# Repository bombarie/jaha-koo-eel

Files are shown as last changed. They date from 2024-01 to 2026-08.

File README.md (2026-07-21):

# Jaha Koo Eel

A robotic remote controlled eel. A prop for the play [Haribo Kimchi](https://www.campo.nu/en/production/24342/haribo_kimchi).

A collaboration between [Adriaan Wormgoor](http://adriaanwormgoor.nl) and [Willem Vooijs](https://willem.vooijs.eu), produced for [Innovation:Lab Theater Utrecht](https://www.theaterutrecht.nl/innovationlab) and [Campo](https://campo.nu).

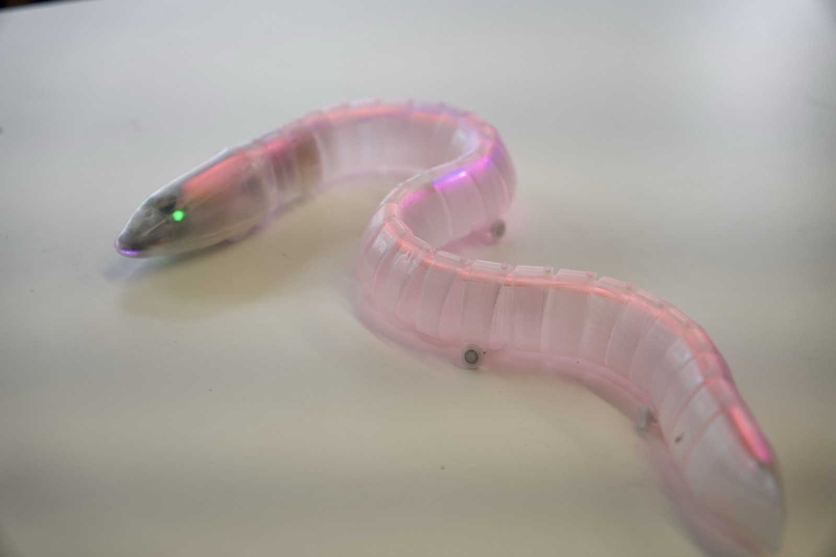
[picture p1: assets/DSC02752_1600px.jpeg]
haribo


## Manual
* [Operator Manual](doc/Haribo%20Kimchi%20Eel%20-%20operator%20manual.pdf)

## Build your own
* [Bill of Materials](./BOM.md)
* [Schematics](doc/Haribo%20Kimchi%20Eel%20-%20tech%20stuff%20-%20visual%20schematic%20and%20pinout.pdf)
* [Code](./arduino/README.md)
* [PCB designs](./kicad/README.md)

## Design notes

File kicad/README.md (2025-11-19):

# PCB Design - quick Links

> 💡 Note the **[libraries](./libraries/)** folder, containing some custom-developed _footprints_ and _symbols_ which are used in various Kicad projects in this repository 

### PCB inside the Eel

[Kicad project](./eel_head_pcbs_assembly//eel_esp32_switch_host_board_v02/)\
[Gerber files](./eel_head_pcbs_assembly/eel_esp32_switch_host_board_v02/_export/gerberfiles/aisler_v01.zip)\
[Schematic](./eel_head_pcbs_assembly/eel_esp32_switch_host_board_v02/_export/schematics/Haribo%20Kimchi%20-%20Eel%20mainboard.pdf)

### PCB inside the GEPRC Tinyradio ELRS r/c transmitter

[Kicad project](./Teensy_32_tx_breakout_board_v2/)\
[Gerber files](./Teensy_32_tx_breakout_board_v2/_export/gerberfiles/jlcpcb_v0.3.zip)\
[Schematic](./Teensy_32_tx_breakout_board_v2/_export/schematics/Teensy%203.2%20host%20pcb.pdf)

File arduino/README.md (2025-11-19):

# Arduino code

All sketches where developed in VSCode using the Platformio plugin.

There's a _lot_ of scrappy test projects, so find below a quick link to the most recent version of key sketches

### Main sketch for Eel microcontroller

[main_seeed_xiao_esp32c3_v2_w_external_files.cpp](./platformio/esp32c3_helloworld/esp32c3_helloworld/src/main_seeed_xiao_esp32c3_v2_w_external_files.cpp)

### Main sketch for Teensy 3.2 inside the GEPRC Tinyradio r/c transmitter

[main.cpp](./platformio/TeensyDuino/src/main.cpp)

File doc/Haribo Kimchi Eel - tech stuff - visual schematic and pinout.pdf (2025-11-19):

# XIAO ESP32-C3

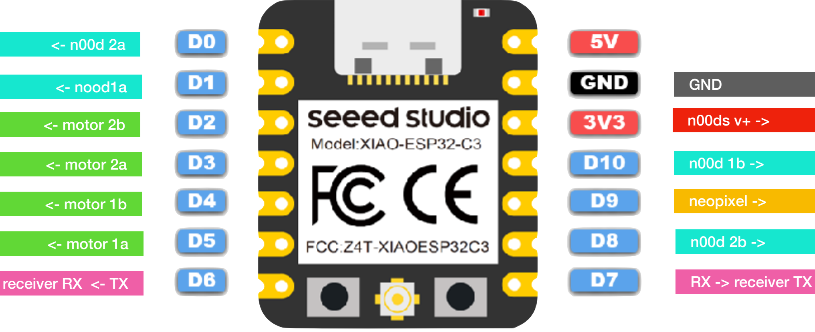
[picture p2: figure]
receiver RX <- TX; RX -> receiver TX; <- motor 2b; <- motor 2a; neopixel ->; <- nood1a
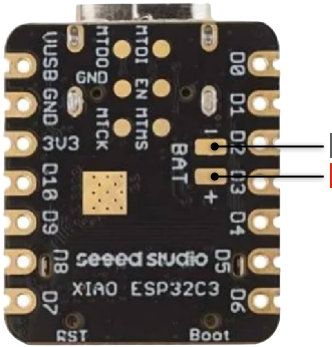
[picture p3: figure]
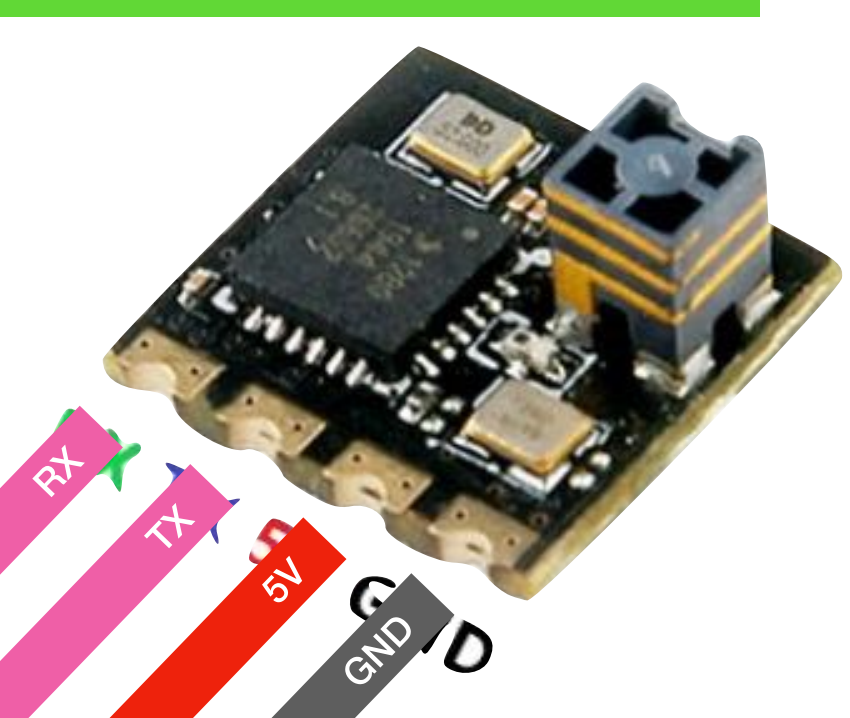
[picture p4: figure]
GND

Bat +

Bat - / GND

<- motor 1b

<- motor 1a

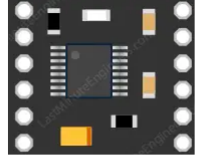
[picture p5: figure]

GND

<- motor 1 +

<- motor 1 -

5V

motor 2b <-

# Generic DRV8833 motor driver

GND
<- motor 2 +

<- motor 2 -

motor 2a <-

motor 1b <-

motor 1a <-

# Happymodel EP2 TXCO ELRS rx

# 600ma 5v boost converter

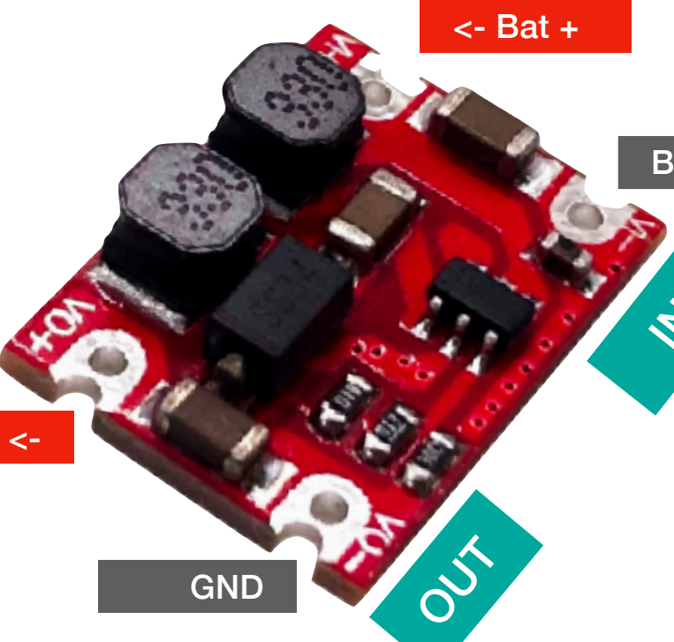
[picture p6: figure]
GND; <- Bat +; OUT

5V <-

Bat GND

IN

# XIAO ESP32-C3

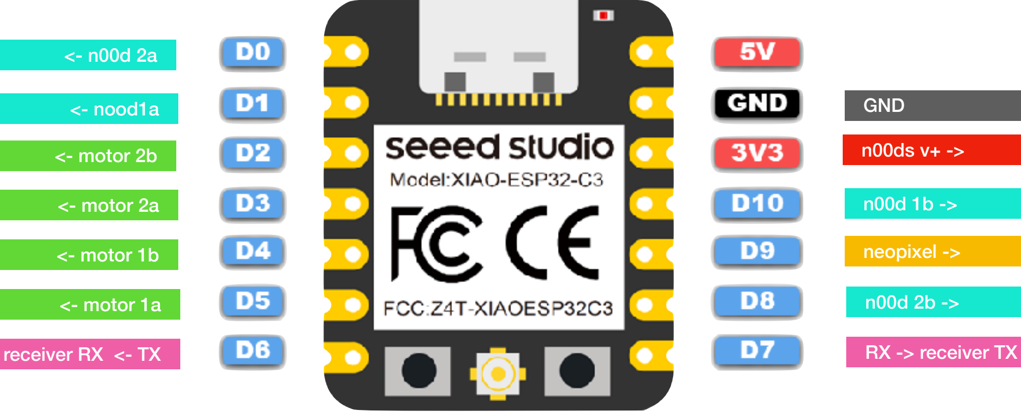
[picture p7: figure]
receiver RX <- TX; RX -> receiver TX; <- motor 2b; <- motor 2a; neopixel ->; <- nood1a
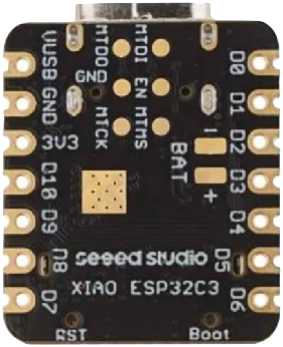
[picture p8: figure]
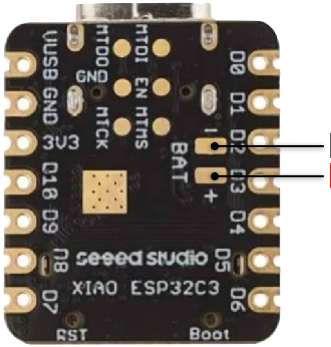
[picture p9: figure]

Bat +

Bat - / GND

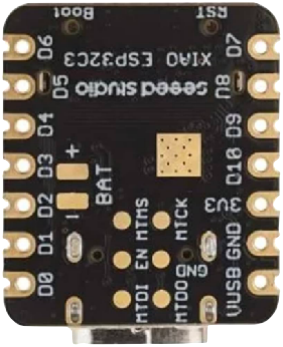
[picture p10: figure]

<- motor 1b

<- motor 1a

GND

<- motor 1b

<- motor 1a

receiver RX <- TX

<- motor 2b

<- motor 2a

<- nood1a

<- n00d 2a

GND

RX -> receiver TX

neopixel ->

n00d 2b ->

n00d 1b ->

n00ds v+ ->

GND

RX -> receiver TX

neopixel ->

n00d 2b ->

n00d 1b ->

n00ds v+ ->

<- motor 1b

<- motor 1a

receiver RX <- TX

<- motor 2b

<- motor 2a

<- nood1a

<- n00d 2a

# Comm protocol of n00ds

# * Midi is 0-127

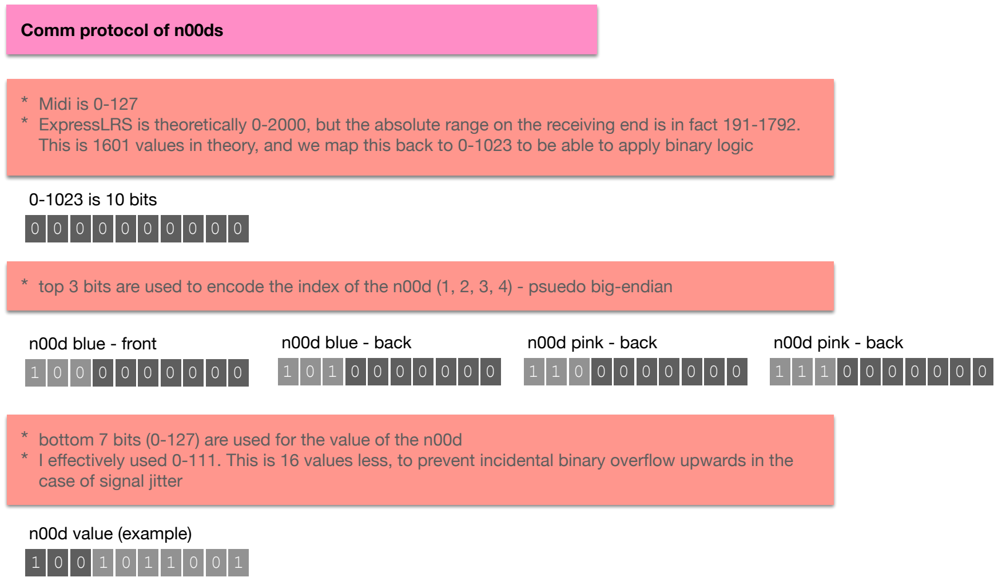
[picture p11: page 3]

0 | 0 | 0 | 0 | 0 | 0 | 0 | 0 | 0 | 0

# 0-1023 is 10 bits

1 | 0 | 0 | 0 | 0 | 0 | 0 | 0 | 0 | 0

# n00d blue - front

1 | 0 | 1 | 0 | 0 | 0 | 0 | 0 | 0 | 0

# n00d blue - back

1 | 1 | 0 | 0 | 0 | 0 | 0 | 0 | 0 | 0

# n00d pink - back

1 | 1 | 1 | 0 | 0 | 0 | 0 | 0 | 0 | 0

# n00d pink - back

* ExpressLRS is theoretically 0-2000, but the absolute range on the receiving end is in fact 191-1792. This is 1601 values in theory, and we map this back to 0-1023 to be able to apply binary logic

# * top 3 bits are used to encode the index of the n00d (1, 2, 3, 4) - psuedo big-endian

# * bottom 7 bits (0-127) are used for the value of the n00d

* I effectively used 0-111. This is 16 values less, to prevent incidental binary overflow upwards in the

# case of signal jitter

1 | 0 | 0 | 1 | 0 | 1 | 1 | 0 | 0 | 1

# n00d value (example)

# AUX4

# AUX3

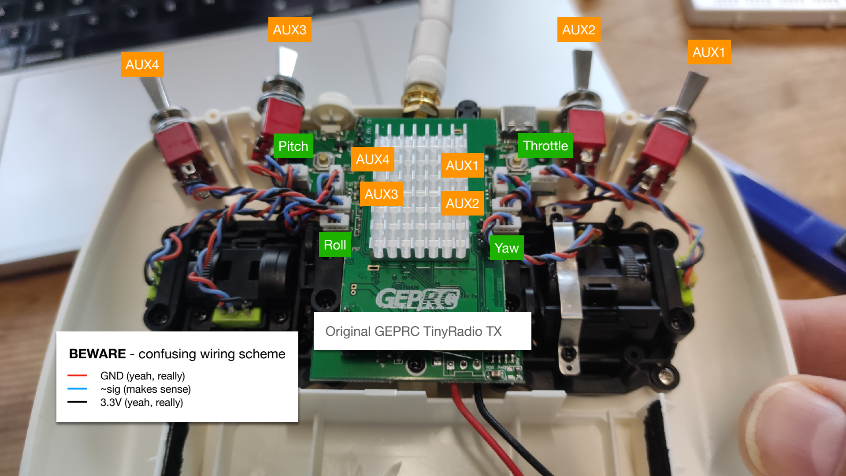
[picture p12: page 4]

# Pitch AUX4

# AUX3

Roll | Yaw

# Throttle AUX1

# AUX1

# AUX2

# AUX2

# Original GEPRC TinyRadio TX BEWARE - confusing wiring scheme

## GND (yeah, really) ~sig (makes sense) 3.3V (yeah, really)

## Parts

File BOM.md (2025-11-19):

# Bill Of Materials

## 3Print files

> 💡 Print all these files in PETG

| Quantity | Model | Color |
| --- | --- | --- |
| 1 | Motor Mount | Transparent |
| 1 | Head Upper | Transparent |
| 1 | Head Lower | Transparent |
| 1 | Switch cap | Transparent |
| 2 | Eye Light Guide | Black |
| 2 | Mouth Light Guide | Black |
| 2 | Front Wheel | Transparent |
| 1 | Tail | Transparent |
| 19 | Segment | Transparent |
| 8 | Segment with n00d | Transparent |
| 1 | Segment battery | Transparent |
| 4 | Axle | Transparent |
| 8 | Wheel | Transparent |

## Non-electronic materials

| Quantity | Component | Comments |
| --- | --- | --- |
| 8 | O-ring for wheels | Transparent silicone |
| 2 | O-ring for front wheels | Transparent silicone |
| 10 | MR63ZZ ball bearings | [link](https://www.amazon.nl/Miniatuur-Kogellagers-Afgeschermde-Afgedichte-3D-Printermodellering/dp/B078RFDJXP/) |

## Electronics

### Eel

#### Mainboard (contains the microcontroller)

[Interactive BOM / connection guide (is handy when assembling)](./kicad/eel_head_pcbs_assembly/eel_esp32_switch_host_board_v02/_export/bom%20(interactive)/ibom.html)

| Quantity | Component | Comments |
| --- | --- | --- |
| 1 | XIAO ESP32-C3 | microcontroller |
| 1 | 100nF capacitor | 0805 SMD |
| 1 | 330ohm resistor | 0805 SMD |
| 1 | 1kohm resistor | 0805 SMD |
| 1 | Nidec 2x03 dpdt CL-SB-22B-11 | SMD, on/off switch, [link](https://nl.rs-online.com/web/p/slide-switches/2443543) |
| 1 | BC817 NPN transistor | SOT-23 |

#### Additional components

| Quantity | Component | Comments |
| --- | --- | --- |
| 2 | N20 motor | Only 3V / 6V motors have sufficient torque. Difficult to find, most motors are 12V |
| 1 | DRV8833 motor driver | [link](https://www.tinytronics.nl/en/mechanics-and-actuators/motor-controllers-and-drivers/stepper-motor-controllers-and-drivers/drv8833-bipolar-stepper-motor-and-dc-motor-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) |
| 1 | DC-DC Step-Up-Down Buck-Boost Converter - 0.6A - 5V Output | [link](https://www.tinytronics.nl/en/power/voltage-converters/buck-boost-(step-up-down)-converters/dc-dc-step-up-down-buck-boost-converter-0.6a-5v-output) |
| 3 | WS2812b rgb led (neopixel) | [link](https://www.hobbyelectronica.nl/product/rgb-led-ws2812b-mini-pcb/) |
| 2 | Nood pink | flexible LED filament - 30cm |
| 2 | Nood blue | flexible LED filament - 30cm |
| 1 | Vapcell INR18350 1100mAh Li-ion battery | [link](https://www.nkon.nl/vapcell-18350-1100-10a.html) |

<!-- DO LATER
### Transmitter

| Quantity | Component | Comments |
| --- | --- | --- |
| | | |
| | | |
-->

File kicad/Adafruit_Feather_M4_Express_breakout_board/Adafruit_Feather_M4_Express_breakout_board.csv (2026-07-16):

Reference | Qty | Value | DNP | Exclude from BOM | Exclude from Board | Footprint | Datasheet
A2 | 1 | Adafruit_Feather_Generic |  |  |  | Module:Adafruit_Feather | https://cdn-learn.adafruit.com/downloads/pdf/adafruit-feather.pdf
C2,C3,C4 | 3 | 1uf |  |  |  | Capacitor_SMD:C_0603_1608Metric | ~
D1 | 1 | LED |  |  |  | LED_SMD:LED_1206_3216Metric | ~
J1,J2,J3,J4,J5 | 5 | Conn_01x03_Female |  |  |  | Connector_JST:JST_SH_BM03B-SRSS-TB_1x03-1MP_P1.00mm_Vertical | ~
R2,R3,R4 | 3 | 10k |  |  |  | Resistor_SMD:R_0603_1608Metric | ~
R5 | 1 | 330 |  |  |  | Resistor_SMD:R_1206_3216Metric | ~

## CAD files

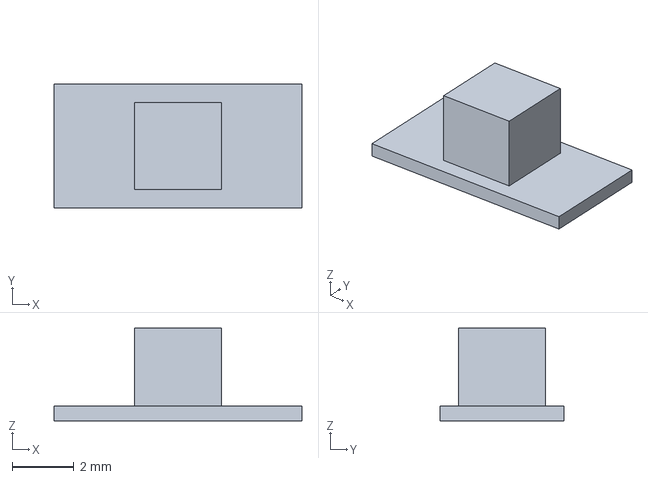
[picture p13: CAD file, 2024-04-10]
CAD/3mf/Main pcb slide switch end cap.3mf
8.00 x 4.00 x 3.00 mm

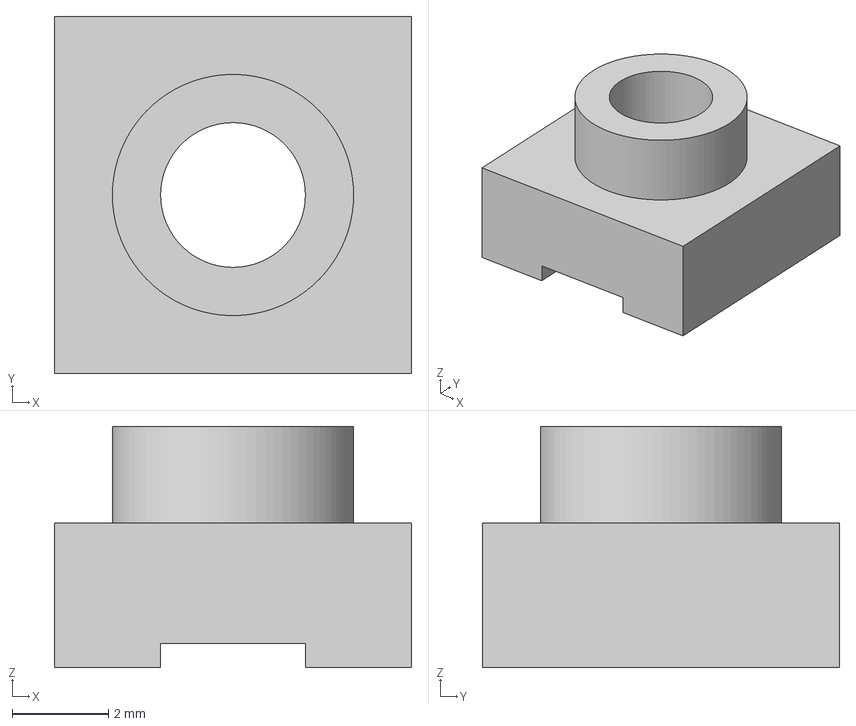
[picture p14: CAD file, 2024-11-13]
CAD/3mf/Eye Light Guide.3mf
7.40 x 7.40 x 5.00 mm

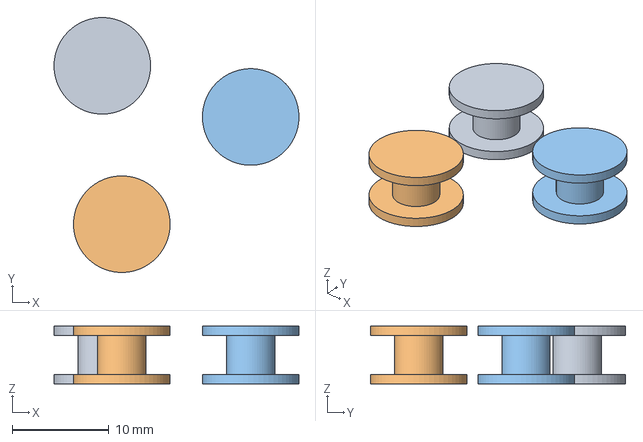
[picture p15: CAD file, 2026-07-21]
CAD/3mf/transmitter/geprc tinyradio - switch cover - 5mm inner diameter.3mf
25.4 x 26.4 x 6.00 mm
switch cover x 3

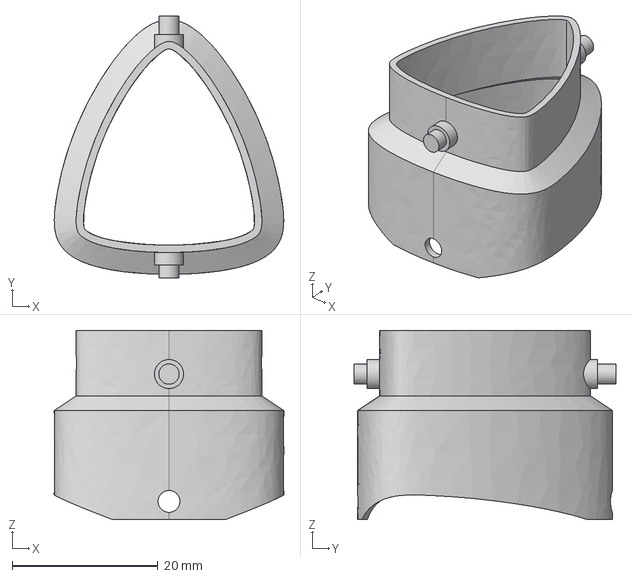
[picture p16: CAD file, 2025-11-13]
CAD/Haribo.step
31.5 x 36.0 x 26.0 mm

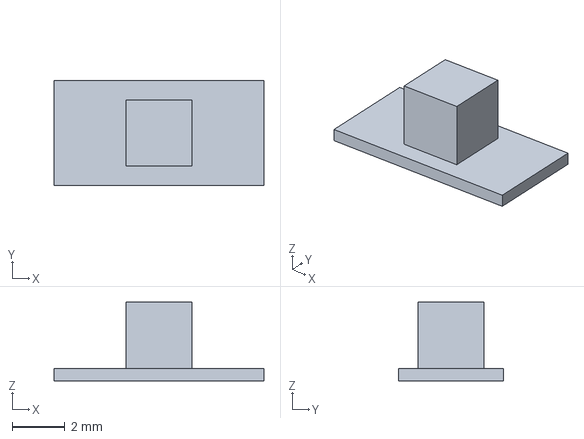
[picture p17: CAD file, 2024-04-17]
CAD/3mf/Switch cap .3mf
8.00 x 4.00 x 3.00 mm

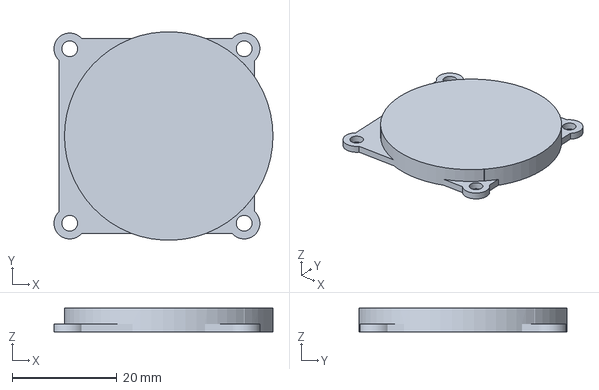
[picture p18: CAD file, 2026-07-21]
CAD/3mf/transmitter/geprc tinyradio - gimbal cover - short.3mf
41.8 x 39.7 x 4.50 mm

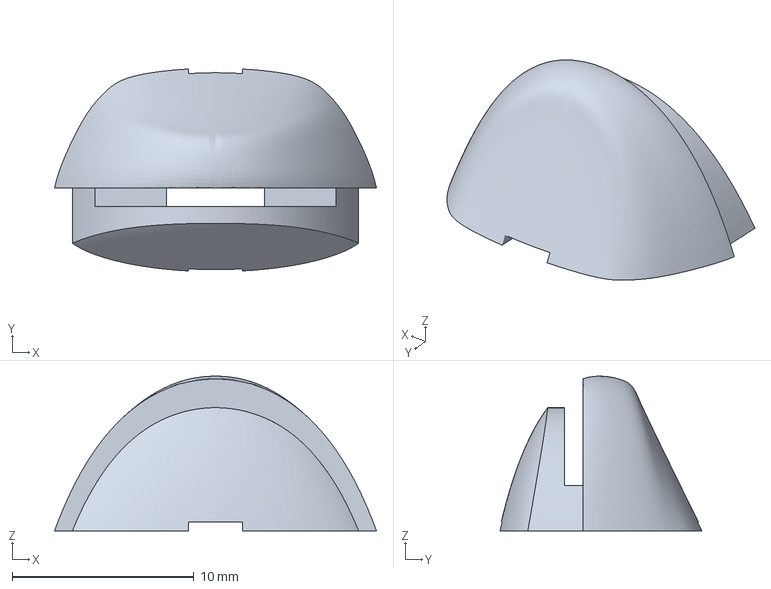
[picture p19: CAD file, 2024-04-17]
CAD/3mf/Mouth Light Guide.3mf
17.7 x 11.1 x 8.52 mm

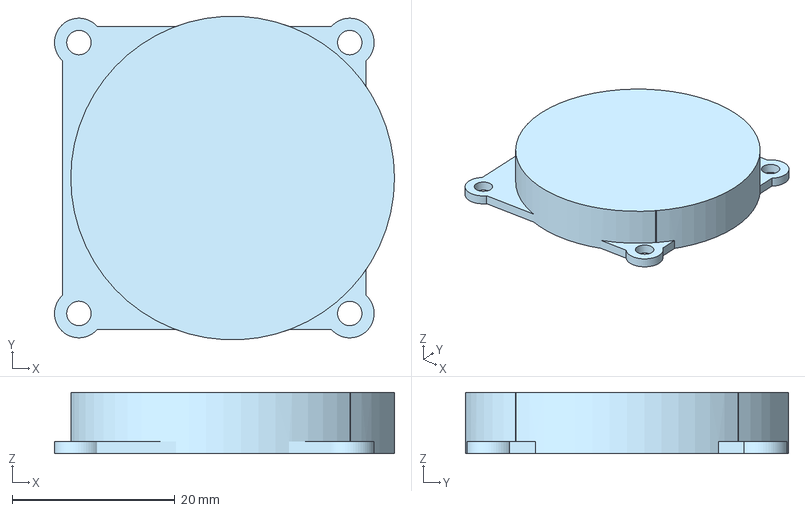
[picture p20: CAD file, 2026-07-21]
CAD/3mf/transmitter/geprc tinyradio - gimbal cover - long.3mf
41.8 x 39.7 x 7.50 mm

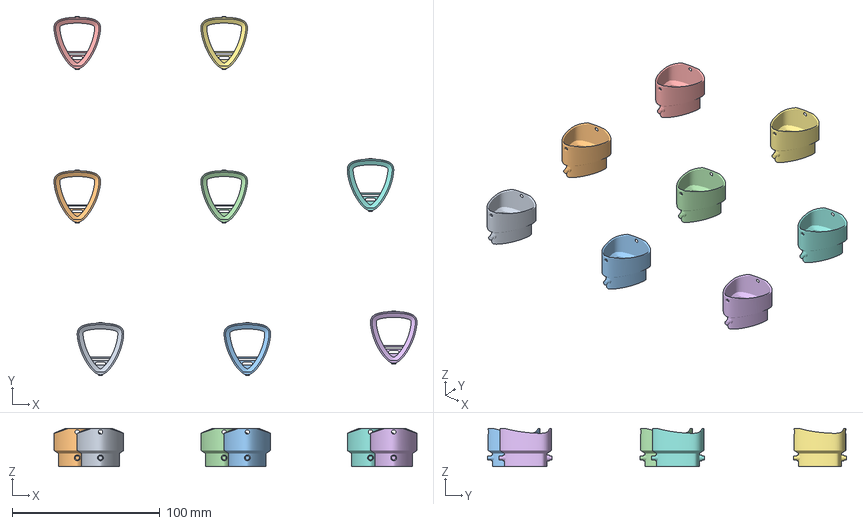
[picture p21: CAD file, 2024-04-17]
CAD/3mf/Segment with n00d.3mf
246.0 x 243.3 x 26.0 mm
Segment (1)
Segment (1) 1 x 2
Segment (1) 2
Segment (1) 3
Segment (1) 4
Segment (1) 5
Segment (1) 6

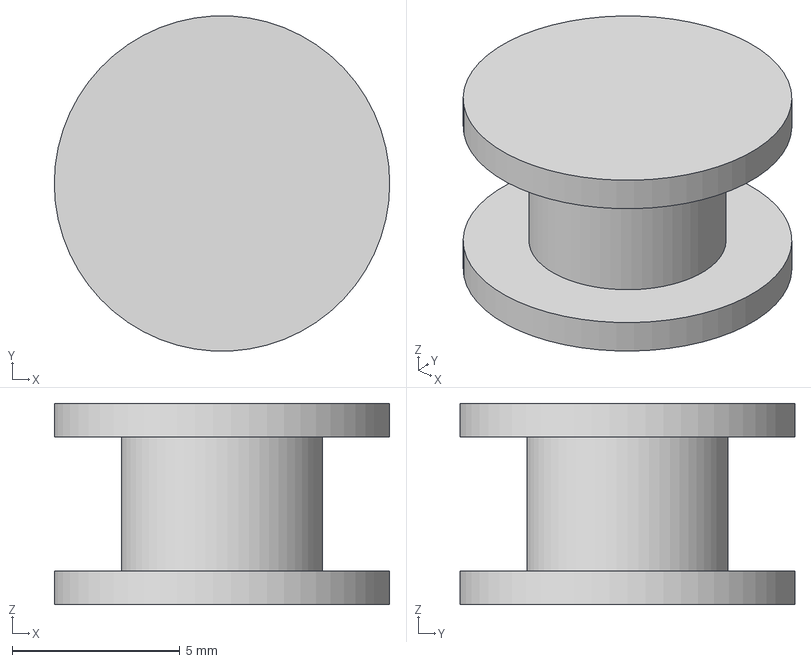
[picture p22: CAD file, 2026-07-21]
CAD/3mf/transmitter/geprc tinyradio - switch cover - 6mm inner diameter.3mf
10.0 x 9.99 x 6.00 mm

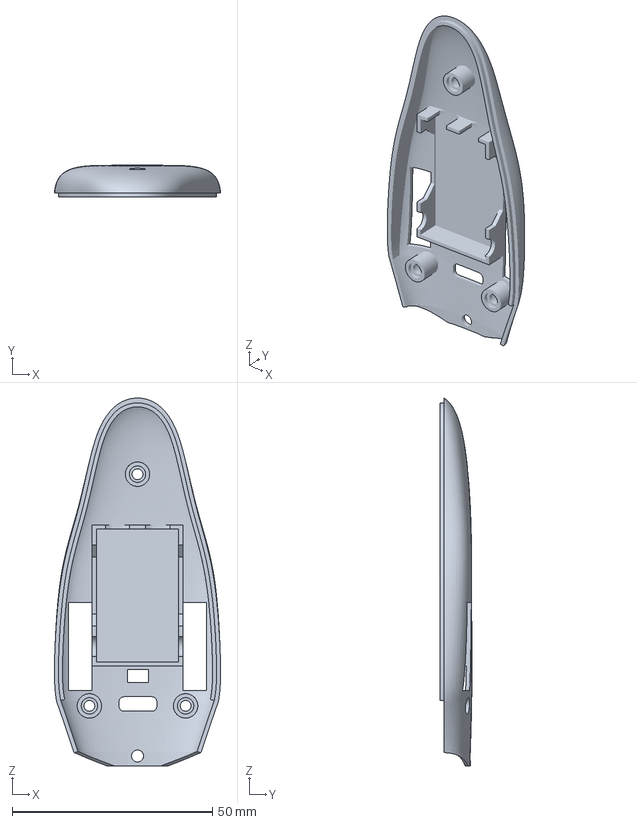
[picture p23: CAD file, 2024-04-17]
CAD/3mf/Head Lower.3mf
41.4 x 8.04 x 91.8 mm

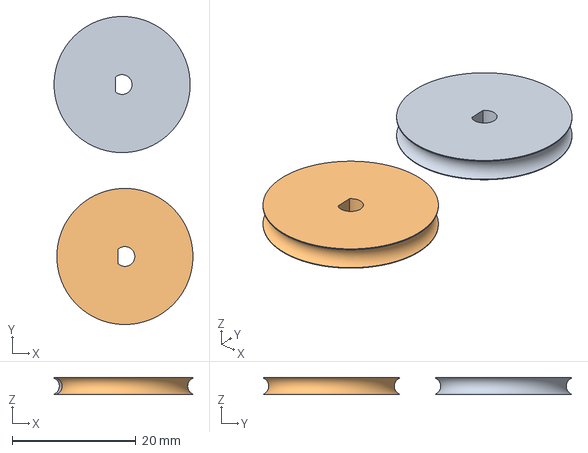
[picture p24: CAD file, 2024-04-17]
CAD/3mf/motor wheel v01.3mf
22.4 x 49.8 x 2.80 mm

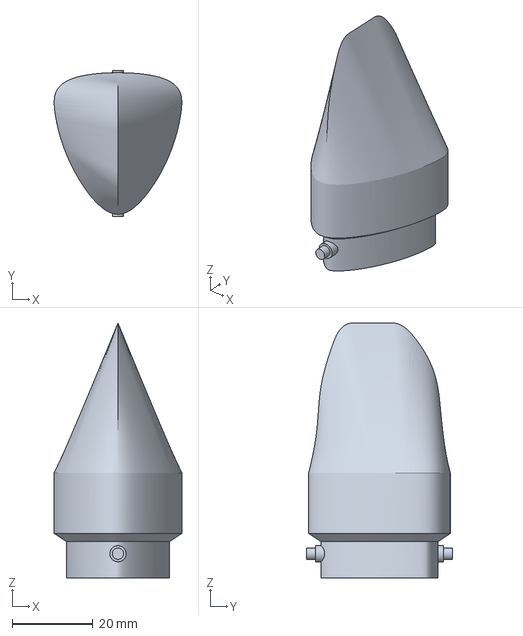
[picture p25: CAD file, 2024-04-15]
CAD/3mf/Tail.3mf
31.5 x 36.0 x 63.0 mm

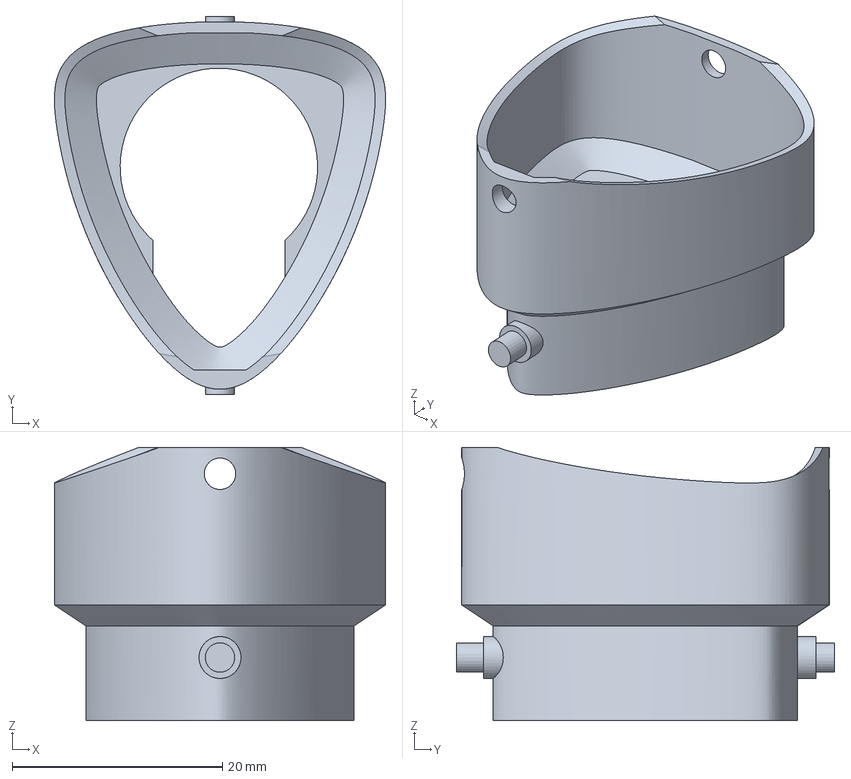
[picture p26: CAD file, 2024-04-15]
CAD/3mf/Segment Battery.3mf
31.5 x 36.0 x 26.0 mm

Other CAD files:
CAD/3mf/Segment.3mf
CAD/3mf/Head Upper.3mf
CAD/3mf/undercarriage wheel.3mf
CAD/3mf/undercarriage axle.3mf
CAD/3mf/Motor Mount.3mf

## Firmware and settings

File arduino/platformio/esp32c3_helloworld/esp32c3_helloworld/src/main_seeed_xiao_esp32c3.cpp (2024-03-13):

#include <Arduino.h>
#include <EelMotor.h>
#include <Wire.h>
#include "sbus.h"
#include <HardwareSerial.h>
#include <Adafruit_NeoPixel.h>
#include <FastLED.h>

// NeoPixel
#define PIN D9
#define NUMPIXELS 3

// When setting up the NeoPixel library, we tell it how many pixels,
// and which pin to use to send signals. Note that for older NeoPixel
// strips you might need to change the third parameter -- see the
// strandtest example for more information on possible values.
Adafruit_NeoPixel pixels(NUMPIXELS, PIN, NEO_GRB + NEO_KHZ800);

HardwareSerial MySerial0(0);

/* SBUS object, reading SBUS */
bfs::SbusRx sbus_rx(&MySerial0, D7, D6, true, false);

/* SBUS data */
bfs::SbusData data;

#define motor1a_pin D5
#define motor1b_pin D4
#define motor2a_pin D3
#define motor2b_pin D2

#define motor1_chan 4 // 6 Channels (ESP32-C3) (0-5) are availible
#define motor2_chan 5 // 6 Channels (ESP32-C3) (0-5) are availible

// setting PWM properties
const uint32_t freq = 2500;
const uint8_t resolution = 8;

EelMotor motor1(motor1a_pin, motor1b_pin, motor1_chan, resolution, freq);
EelMotor motor2(motor2a_pin, motor2b_pin, motor2_chan, resolution, freq);

u_long sbusPrevPacketTime;
bool sbusLost = false;

#define SBUS_VAL_MIN 191
#define SBUS_VAL_MAX 1793
#define SBUS_VAL_CENTER 992
#define SBUS_VAL_DEADBAND 6
#define SBUS_LOST_TIMEOUT 100
#define SBUS_SWITCH_MIN 192
#define SBUS_SWITCH_MAX 1792
#define SBUS_SWITCH_MIN_THRESHOLD 1400
#define SBUS_SWITCH_MAX_THRESHOLD 550

#define TX_ROLL 0
#define TX_PITCH 1
#define TX_THROTTLE 2
#define TX_YAW 3
#define TX_AUX1 4
#define TX_AUX2 5
#define TX_AUX3 6
#define TX_AUX4 7

enum HEAD_STATE
{
  STATE_1,
  STATE_2,
  STATE_3
};
HEAD_STATE headState = STATE_1;

enum BODY_STATE
{
  NOOD1,
  NOOD2,
  BOTH_NOODS
};
BODY_STATE bodyState = BOTH_NOODS;

// The CONNECTION_ESTABLISHED and CONNECTION_LOST states are kind of vanity states, in case I want to
// implement some kind of unique visual feedback for when the connection is lost or established.
enum CONNECTION_STATE
{
  DISCONNECTED,
  CONNECTION_ESTABLISHED,
  CONNECTION_LOST,
  CONNECTED
};
CONNECTION_STATE connectionState = DISCONNECTED;

#define SBUS_PACKET_PRINT_INTERVAL 100 // ms
u_long sbusPacketPrintPrevTime = 0;

float sinCounter = 0.0;
float sinCounterIncrement = 0.05;

bool doSineMovement = false;

byte hVal = 0;
byte vVal = 0;

int16_t motor1Val;
int16_t motor2Val;

int16_t n00d1a, n00d1b, n00d2a, n00d2b;
uint16_t throttle, throttleAdjusted;

int16_t noodVals[] = {0, 0, 0, 0};
int16_t noodAvgVals[] = {0, 0, 0, 0};
uint16_t n00dSegmentIdentifiers[] = {512, 640, 768, 896};

#define n00d_1a_Pin D8
#define n00d_1b_Pin D1
#define n00d_2a_Pin D10
#define n00d_2b_Pin D0

static const uint8_t nood1a_chan = 0;
static const uint8_t nood1b_chan = 1;
static const uint8_t nood2a_chan = 2;
static const uint8_t nood2b_chan = 3;

void initNoods();
void initPixels();
void updateBodyLightValues();
void setBodyLights();
void updateSerialIO();
void checkIncomingSerial();
void setn00d(uint8_t chan, uint8_t val);

void resetSbusData();
void setRGBLights();
void updateHeadBodyLights_disconnected();

// define methods
void driveMotors();
void parseSBUS(bool serialPrint);
void updateHeadBodyState();
void updateHeadLightValues();
void setBodyLights();
void calcMotorValues();

void setup()
{
  Serial.begin(115200);

  /* Begin the SBUS communication */
  sbus_rx.Begin();
  // sbus_tx.Begin();

  initNoods();

  motor1.reversed = true;
  motor2.reversed = true;

  // by default, let's have the program assume sbus is lost
  sbusPrevPacketTime = -SBUS_LOST_TIMEOUT;

  initPixels();

  Serial.println("Hello World!");
}

void loop()
{
  // pixels.clear(); // Set all pixel colors to 'off'

  // read SBUS
  parseSBUS(false);

  // determine how to set the head and body lights
  switch (connectionState)
  {
  case DISCONNECTED:
    resetSbusData();
    updateHeadBodyLights_disconnected();
    break;
  case CONNECTION_ESTABLISHED:
    if (sbusLost)
    {
      connectionState = CONNECTION_LOST;
    }
    else
    {
      connectionState = CONNECTED;
    }
    break;
  case CONNECTION_LOST:
    if (!sbusLost)
    {
      connectionState = CONNECTION_ESTABLISHED;
    }
    break;
  case CONNECTED:
    if (sbusLost)
    {
      connectionState = CONNECTION_LOST;
    }
    break;
  }

  updateHeadBodyState();

  updateBodyLightValues();
  setBodyLights();

  updateHeadLightValues();
  // setBodyLights();

  calcMotorValues();
  driveMotors();

  // delay a little.
  delay(1000 / 200);
}

void initNoods()
{
  pinMode(n00d_1a_Pin, OUTPUT);
  pinMode(n00d_1b_Pin, OUTPUT);
  pinMode(n00d_2a_Pin, OUTPUT);
  pinMode(n00d_2b_Pin, OUTPUT);

  // nood 1a
  ledcSetup(nood1a_chan, freq, resolution);
  ledcAttachPin(n00d_1a_Pin, nood1a_chan);

  // nood 1b
  ledcSetup(nood1b_chan, freq, resolution);
  ledcAttachPin(n00d_1b_Pin, nood1b_chan);

  // nood 2a
  ledcSetup(nood2a_chan, freq, resolution);
  ledcAttachPin(n00d_2a_Pin, nood2a_chan);

  // nood 2b
  ledcSetup(nood2b_chan, freq, resolution);
  ledcAttachPin(n00d_2b_Pin, nood2b_chan);

  setn00d(nood1a_chan, 0);
  setn00d(nood1b_chan, 0);
  setn00d(nood2a_chan, 0);
  setn00d(nood2b_chan, 0);
}

void initPixels()
{
  pixels.begin(); // INITIALIZE NeoPixel strip object (REQUIRED)
  delay(10);
  pixels.clear();
  pixels.show();
}

void updateBodyLightValues()
{
  // map throttle range to 0-1023
  throttle = map(data.ch[TX_THROTTLE], SBUS_VAL_MIN, SBUS_VAL_MAX, 0, 1023);

  throttleAdjusted = 0; // used to store the adjusted throttle value

  // if (throttle & (0x1 << 9)) // 512
  // if (throttle & n00dSegmentIdentifiers[0] == n00dSegmentIdentifiers[0]) // 512
  if (throttle >> 7 == 0x4) // 0b100
  {
    // throttleAdjusted = throttle - (throttle >> 5);
    throttleAdjusted = throttle - 9;
    n00d1a = (throttle & 0x7E) - 9;
    n00d1a = map(constrain(n00d1a, 0, 55), 0, 55, 0, 255);
  }
  // if (throttle & (0x1 << 8)) // 256
  // if (throttle & n00dSegmentIdentifiers[1] == n00dSegmentIdentifiers[1]) // 640
  if (throttle >> 7 == 0x5) // 0b101
  {
    // throttle -= throttle - (throttle >> 5);
    throttleAdjusted = throttle - 10;
    n00d1b = (throttle & 0x7E) - 10;
    n00d1b = map(constrain(n00d1b, 0, 55), 0, 55, 0, 255);
  }
  // if (throttle & (0x1 << 7)) // 128
  // if (throttle & n00dSegmentIdentifiers[2] == n00dSegmentIdentifiers[2]) // 768
  if (throttle >> 7 == 0x6) // 0b110
  {
    throttleAdjusted = throttle - 9;
    n00d2a = (throttle & 0x7E) - 9;
    n00d2a = map(constrain(n00d2a, 0, 55), 0, 55, 0, 255);
  }
  // if (throttle & (0x1 << 6)) // 64
  // if (throttle & n00dSegmentIdentifiers[3] == n00dSegmentIdentifiers[3]) // 896
  if (throttle >> 7 == 0x7) // 0b111
  {
    throttleAdjusted = throttle - 9;
    n00d2b = (throttle & 0x7E) - 9;
    n00d2b = map(constrain(n00d2b, 0, 55), 0, 55, 0, 255);
  }

  noodVals[0] = n00d1a;
  noodVals[1] = n00d1b;
  noodVals[2] = n00d2a;
  noodVals[3] = n00d2b;

  noodAvgVals[0] = 0.85 * noodAvgVals[0] + 0.15 * noodVals[0];
  noodAvgVals[1] = 0.85 * noodAvgVals[1] + 0.15 * noodVals[1];
  noodAvgVals[2] = 0.85 * noodAvgVals[2] + 0.15 * noodVals[2];
  noodAvgVals[3] = 0.85 * noodAvgVals[3] + 0.15 * noodVals[3];
}

void setBodyLights()
{
  setn00d(nood1a_chan, noodAvgVals[0]);
  setn00d(nood1b_chan, noodAvgVals[1]);
  setn00d(nood2a_chan, noodAvgVals[2]);
  setn00d(nood2b_chan, noodAvgVals[3]);
}

uint8_t channelToPrint = 255;
void updateSerialIO()
{
  checkIncomingSerial();

  EVERY_N_MILLIS(100)
  {
    if (channelToPrint == 0) // only nood1a
    {
      Serial.print("n00d1a: ");
      Serial.print(n00d1a);
      Serial.print("\t in binary: ");
      Serial.println(n00d1a, BIN);
    }
    if (channelToPrint == 1) // only nood1b
    {
      Serial.print("n00d1b: ");
      Serial.print(n00d1b);
      Serial.print("\t in binary: ");
      Serial.println(n00d1b, BIN);
    }
    if (channelToPrint == 2) // only nood2a
    {
      if (throttle & (0x1 << 7)) // 128
      {
        Serial.print("TX_THROTTLE: ");
        Serial.print(data.ch[TX_THROTTLE]);
        Serial.print("\t throttle: ");
        Serial.print(throttle);
        Serial.print("\t (in binary: ");
        Serial.print(throttle, BIN);
      }
      Serial.print("\t n00d2a: ");
      Serial.print(n00d2a);
      Serial.print("\t in binary: ");
      Serial.println(n00d2a, BIN);
    }
    if (channelToPrint == 3) // only nood2b
    {
      if (throttle & (0x1 << 6)) // 64
      {
        Serial.print("TX_THROTTLE: ");
        Serial.print(data.ch[TX_THROTTLE]);
        Serial.print("\t throttle: ");
        Serial.print(throttle);
        Serial.print("\t (in binary: ");
        Serial.print(throttle, BIN);
      }
      Serial.print("n00d2b: ");
      Serial.print(n00d2b);
      Serial.print("\t in binary: ");
      Serial.println(n00d2b, BIN);
    }
    if (channelToPrint == 100) // everything
    {
      Serial.print("TX_THROTTLE: ");
      Serial.print(data.ch[TX_THROTTLE]);
      Serial.print("\t throttle: ");
      Serial.print(throttle);
      Serial.print("\t (in binary: ");
      Serial.println(throttle, BIN);
      Serial.print("n00d1a: ");
      Serial.print(n00d1a);
      Serial.print("\t n00d1b: ");
      Serial.print(n00d1b);
      Serial.print("\t n00d2a: ");
      Serial.print(n00d2a);
      Serial.print("\t n00d2b: ");
      Serial.println(n00d2b);
      Serial.println("");
    }
  }
}

void checkIncomingSerial()
{
  if (Serial.available() > 0)
  {
    char inChar = Serial.read();
    switch (inChar)
    {
    case '1':
      channelToPrint = 0;
      break;
    case '2':
      channelToPrint = 1;
      break;
    case '3':
      channelToPrint = 2;
      break;
    case '4':
      channelToPrint = 3;
      break;
    case 'a':
      channelToPrint = 100;
      break;
    case 'x':
      channelToPrint = 255;
      break;
    }

    while (Serial.available() > 0)
    {
      Serial.read();
    }
  }
}

void setn00d(uint8_t chan, uint8_t val)
{
  ledcWrite(chan, (255 - val));
}

void parseSBUS(bool serialPrint)
{
  if (sbus_rx.Read())
  {
    sbusPrevPacketTime = millis();
    if (connectionState == CONNECTION_LOST || connectionState == DISCONNECTED)
    {
      Serial.println("Regained SBUS connection");
      connectionState = CONNECTED;
    }

    /* Grab the received data */
    data = sbus_rx.data();

    /* Display the received data */
    if (millis() - sbusPacketPrintPrevTime > SBUS_PACKET_PRINT_INTERVAL)
    {
      //*
      if (Serial && serialPrint)
      {
        for (int8_t i = 0; i < data.NUM_CH; i++)
        {
          Serial.print(data.ch[i]);
          Serial.print("\t");
        }
        Serial.println();
      }
      //*/

      sbusPacketPrintPrevTime = millis();
    }
  }

  // if SBUS lost, reset the channels
  if (millis() - sbusPrevPacketTime > SBUS_LOST_TIMEOUT)
  {
    if (connectionState != DISCONNECTED)
    {
      Serial.print("Lost SBUS connection >> setting throttle/pitch/roll to ");
      Serial.print((SBUS_VAL_MIN + SBUS_VAL_MAX) / 2);
      Serial.println(" and yaw to 0 ");

      connectionState = DISCONNECTED;
    }
  }

  // if (connectionState == CONNECTION_LOST)
  // {
  //   resetSbusData();
  // }
}

void resetSbusData()
{
  for (int8_t i = 0; i < data.NUM_CH; i++)
  {
    data.ch[i] = SBUS_VAL_MIN;
    if (i < 4)
    {
      data.ch[i] = (SBUS_VAL_MIN + SBUS_VAL_MAX) / 2;
      if (i == TX_YAW)
        data.ch[i] = SBUS_VAL_MIN;
    }
  }
}

void updateHeadBodyState()
{
  // if (data.ch[TX_AUX2] < SBUS_SWITCH_MIN_THRESHOLD)
  // {
  //   headState = STATE_1;
  // }
  // else
  // {
  //   headState = STATE_2;
  // }

  if (data.ch[TX_AUX2] > SBUS_SWITCH_MIN_THRESHOLD)
  {
    headState = STATE_1;
  }
  else if (data.ch[TX_AUX2] > SBUS_SWITCH_MAX_THRESHOLD)
  {
    headState = STATE_2;
  }
  else
  {
    headState = STATE_3;
  }
}

// led 1 and 3 = eyes
// led 2 = mouth
void updateHeadLightValues()
{
  uint8_t audioVal = constrain(map(data.ch[TX_YAW], SBUS_VAL_MIN, SBUS_VAL_MAX, 0, 255), 0, 255);
  switch (headState)
  {
  case STATE_1: // tmp: off
    pixels.setPixelColor(0, pixels.Color(0, 0, 0)); // left eye
    pixels.setPixelColor(1, pixels.Color(0, 0, 0)); // mouth
    pixels.setPixelColor(2, pixels.Color(0, 0, 0)); // right eye
    // pixels.setPixelColor(0, pixels.Color(255, 0, 0)); // left eye
    // pixels.setPixelColor(1, pixels.Color(255, audioVal, audioVal)); // mouth
    // pixels.setPixelColor(2, pixels.Color(audioVal, 255, audioVal)); // right eye
    break;
  case STATE_2: // tmp: green
    pixels.setPixelColor(0, pixels.Color(0, audioVal, 0)); // left eye
    pixels.setPixelColor(1, pixels.Color(0, audioVal, 0));      // mouth
    pixels.setPixelColor(2, pixels.Color(0, audioVal, 0)); // right eye
    // pixels.setPixelColor(0, pixels.Color(audioVal, audioVal, audioVal)); // left eye
    // pixels.setPixelColor(1, pixels.Color(255, audioVal, audioVal));      // mouth
    // pixels.setPixelColor(2, pixels.Color(audioVal, audioVal, audioVal)); // right eye
    break;
  case STATE_3: // tmp: white
    pixels.setPixelColor(0, pixels.Color(audioVal, audioVal, audioVal)); // left eye
    pixels.setPixelColor(1, pixels.Color(audioVal, audioVal, audioVal));      // mouth
    pixels.setPixelColor(2, pixels.Color(audioVal, audioVal, audioVal)); // right eye
    // pixels.setPixelColor(0, pixels.Color(audioVal, audioVal, audioVal)); // left eye
    // pixels.setPixelColor(1, pixels.Color(255, audioVal, audioVal));      // mouth
    // pixels.setPixelColor(2, pixels.Color(audioVal, audioVal, audioVal)); // right eye
    break;
  }
  pixels.show(); // Send the updated pixel colors to the hardware.
}

void setRGBLights()
{
  // ??
}

void updateHeadBodyLights_disconnected()
{
  // ??
}

void calcMotorValues()
{
  byte motorPowerRange = 255;

  /* position of AUX4 selects diff motor power ranges
  if (data.ch[TX_AUX4] > SBUS_SWITCH_MIN_THRESHOLD)
  {
    motorPowerRange = 255;
  }
  else if (data.ch[TX_AUX4] > SBUS_SWITCH_MAX_THRESHOLD)
  {
    motorPowerRange = 130;
  }
  else
  {
    motorPowerRange = 80;
  }
  //*/

  byte motorOutMode = 0;
  int16_t mix = 1000;
  //* position of AUX4 selects diff motor output modes
  if (data.ch[TX_AUX4] > SBUS_SWITCH_MIN_THRESHOLD)
  {
    motorOutMode = 0;
  }
  else if (data.ch[TX_AUX4] > SBUS_SWITCH_MAX_THRESHOLD)
  {
    motorOutMode = 1;
  }
  else
  {
    motorOutMode = 2;
  }

  if (motorOutMode == 0)
  {

    //*/
    motor1Val = constrain(map(data.ch[TX_PITCH], SBUS_VAL_MIN, SBUS_VAL_MAX, -motorPowerRange, motorPowerRange), -255, 255);
    motor2Val = motor1Val;

    int16_t throttleVal = motor1Val;
    EVERY_N_MILLIS(250)
    {
      // Serial.print("motorPowerRange: " + String(motorPowerRange));
      // Serial.println(", throttleVal: " + String(motor2Val));
    }

    // float mix = constrain(map(data.ch[TX_ROLL], SBUS_VAL_MIN, SBUS_VAL_MAX, 0, 1000), 750, 250) / 1000.0; // gives a range of .25-.75

    // /*
    // range 0.0-1.0, then an exponent, then map to 250-750
    mix = constrain(map(data.ch[TX_ROLL], SBUS_VAL_MIN, SBUS_VAL_MAX, 0, 2000), 0, 2000); // gives a range of 0-2000
    // mix = pow(mix, 1.4);
    // mix = map((mix * 1000.0), 1000, 0, 250, 750) / 1000.0; // reverse the input range because we want to reverse the steering
    // mix = map((mix * 1000.0), 1000, 0, 0, 1000) / 1000.0; // reverse the input range because we want to reverse the steering
    //*/

    motor1Val = (int16_t)((throttleVal * (2000 - mix)) / 2000);
    motor2Val = (int16_t)((throttleVal * mix) / 2000);
  }
  if (motorOutMode == 1)
  {
    motor1Val = 0;
    motor2Val = 0;
    if (abs(data.ch[TX_PITCH] - SBUS_VAL_CENTER) > 200)
    {
      // if forward or backward: move linearly (no mixing)

      motor1Val = constrain(map(data.ch[TX_PITCH], SBUS_VAL_MIN, SBUS_VAL_MAX, -motorPowerRange, motorPowerRange), -255, 255);
      motor2Val = constrain(map(data.ch[TX_PITCH], SBUS_VAL_MIN, SBUS_VAL_MAX, -motorPowerRange, motorPowerRange), -255, 255);
    }
    else
    {
      // if left/right: only left or right, no mixing
      if (data.ch[TX_ROLL] < (SBUS_VAL_CENTER - 150)) // left
      {
        motor2Val = 0;
        motor1Val = constrain(map(data.ch[TX_ROLL], SBUS_VAL_CENTER, SBUS_VAL_MIN, 0, motorPowerRange), 0, 255);
      }
      if (data.ch[TX_ROLL] > (SBUS_VAL_CENTER + 150)) // right
      {
        motor2Val = constrain(map(data.ch[TX_ROLL], SBUS_VAL_CENTER, SBUS_VAL_MAX, 0, motorPowerRange), 0, 255);
        motor1Val = 0;
      }
    }
  }
  if (motorOutMode == 2)
  {
    motor1Val = 0;
    motor2Val = 0;
    if (abs(data.ch[TX_PITCH] - SBUS_VAL_CENTER) > 200)
    {
      // if forward or backward: move linearly (no mixing)

      motor1Val = constrain(map(data.ch[TX_PITCH], SBUS_VAL_MIN, SBUS_VAL_MAX, -motorPowerRange, motorPowerRange), -255, 255);
      motor2Val = constrain(map(data.ch[TX_PITCH], SBUS_VAL_MIN, SBUS_VAL_MAX, -motorPowerRange, motorPowerRange), -255, 255);
    }
    else
    {
      motor1Val = constrain(map(data.ch[TX_ROLL], SBUS_VAL_MIN, SBUS_VAL_MAX, -motorPowerRange, motorPowerRange), -255, 255);
      motor2Val = constrain(map(data.ch[TX_ROLL], SBUS_VAL_MIN, SBUS_VAL_MAX, motorPowerRange, -motorPowerRange), -255, 255);
    }
  }

  /*
  doSineMovement = (data.ch[TX_AUX4] < SBUS_SWITCH_MIN_THRESHOLD) ? true : false;
  doSineMovement = false; // override

  // only applies if doSineMovement is true
  // sinCounterIncrement = map(data.ch[TX_THROTTLE], SBUS_VAL_MIN, SBUS_VAL_MAX, 200, 1000) / 5000.0;
  sinCounterIncrement = 550 / 5000.0; // override for testing
  float sinMulFactor = .9;
  sinMulFactor = constrain(map(data.ch[TX_AUX3], SBUS_VAL_MIN, SBUS_VAL_MAX, 450, 900), 450, 900) / 1000.0;
  float sinMult1 = sin(sinCounter) * sinMulFactor + (1.0 - sinMulFactor);
  float sinMult2 = sin(sinCounter + PI) * sinMulFactor + (1.0 - sinMulFactor);
  sinCounter += sinCounterIncrement;
  // Serial.println("sinCounterIncrement: " + String(sinCounterIncrement));

  if (doSineMovement)
  {
    float ampMul = constrain(map(data.ch[TX_AUX4], SBUS_VAL_MIN, SBUS_VAL_MAX, 0, 1000), 0, 1000) / 1000.0;
    motor1Val *= (sinMult1 * ampMul) + (1.0 - ampMul);
    motor2Val *= (sinMult2 * ampMul) + (1.0 - ampMul);
  }
  //*/

  motor1Val = constrain(motor1Val, -255, 255);
  motor2Val = constrain(motor2Val, -255, 255);

  EVERY_N_MILLIS(200)
  {
    Serial.println("mix: " + String(mix) + ", motor1Val: " + String(motor1Val) + ", motor2Val: " + String(motor2Val) + ", motor1._pwmVal: " + String(motor1._pwmVal) + ", motor2._pwmVal: " + String(motor2._pwmVal));
  }
}

void driveMotors()
{
  // MOTOR 1
  if (abs(motor1Val) < SBUS_VAL_DEADBAND)
  {
    motor1.motorStop(); // Soft Stop    -no argument
  }
  if (motor1Val < -SBUS_VAL_DEADBAND)
  {
    motor1.motorRev(-motor1Val); // Pass the speed to the motor: 0-255 for 8 bit resolution
  }
  if (motor1Val > SBUS_VAL_DEADBAND)
  {
    motor1.motorGo(motor1Val); // Pass the speed to the motor: 0-255 for 8 bit resolution
  }

  // MOTOR 2
  if (abs(motor2Val) < SBUS_VAL_DEADBAND)
  {
    motor2.motorStop(); // Soft Stop    -no argument
  }
  if (motor2Val < -SBUS_VAL_DEADBAND)
  {
    motor2.motorRev(-motor2Val); // Pass the speed to the motor: 0-255 for 8 bit resolution
  }
  if (motor2Val > SBUS_VAL_DEADBAND)
  {
    motor2.motorGo(motor2Val); // Pass the speed to the motor: 0-255 for 8 bit resolution
  }
}

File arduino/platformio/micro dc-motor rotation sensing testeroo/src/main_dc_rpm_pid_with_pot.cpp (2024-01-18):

#include <Arduino.h>
#include <MX1508.h>
// #include <PID_v1.h>
#include "ArduPID.h"

/*
  2023-01-04 -  MEH.... how the fuck does this PID stuff work? I'm using Teleplot to plot the values. I can't seem to get a good working system going.
                The pid controller appears to work fine above ~115rpm. Lower than that the output rpm just doesn't seem to approximate the setpoint. Wha? 
                Does it have something to do with the bias setting? I don't quite get that one....
                Leaving this for now -> it's of later concern
*/

#define MOTOR_PIN_A 5
#define MOTOR_PIN_B 6

// MX1508 schematics(in Chinese) can be found here at: http://sales.dzsc.com/486222.html
/*
 * MX1508(uint8_t pinIN1, uint8_t pinIN2, DecayMode decayMode, NumOfPwmPins numPWM);
 * DecayMode must be FAST_DECAY or SLOW_DECAY,
 * NumOfPwmPins, either use 1 or 2 pwm.
 * I recommend using 2 pwm pins per motor so spinning motor forward and backward gives similar response.
 * if using 1 pwm pin, make sure its pinIN1, then set pinIN2 to any digital pin. I dont recommend this setting because
 * we need to use FAST_DECAY in one direction and SLOW_DECAY for the other direction.
 */
// MX1508 motorA(MOTOR_PIN_A,MOTOR_PIN_B, FAST_DECAY, NUMPWM);
MX1508 motorA(MOTOR_PIN_A, MOTOR_PIN_B);
#define MAX_RPM 130

// define methods
void interruptA();

#define LED_PIN 13

#define SETPOINT_POT_PIN A0
#define Pterm_POT_PIN A1
#define Iterm_POT_PIN A2
#define Dterm_POT_PIN A5

#define MOTOR_ENCODER_A_PIN 2
#define MOTOR_ENCODER_B_PIN 3

// timer stuff
uint32_t prevChangeRPM;
uint8_t rpmType = 0;

// update rpm-print stuff
uint32_t prevPrintRPM;

uint16_t rpmTarget = 0;

volatile float RPM = 0;
volatile float RPM_SMOOTH = 0;
volatile uint32_t lastA = 0;
volatile bool motordir = true;
volatile uint16_t encoderCount = 0;
volatile float revs = 0.0;
volatile uint16_t interruptCount = 0;

// Define Variables we'll be connecting to
double Setpoint, Input, Output;

// Specify the links and initial tuning parameters
double Kp = 2, Ki = 4, Kd = 1;
ArduPID myController;

// These let us convert ticks-to-RPM
#define GEARING 20
#define ENCODERMULT 12

void setup()
{
  Serial.begin(115200);

  pinMode(LED_PIN, OUTPUT);
  digitalWrite(LED_PIN, LOW);

  pinMode(MOTOR_ENCODER_A_PIN, INPUT_PULLUP);
  pinMode(MOTOR_ENCODER_B_PIN, INPUT_PULLUP);
  attachInterrupt(digitalPinToInterrupt(MOTOR_ENCODER_A_PIN), interruptA, RISING);

  myController.begin(&Input, &Output, &Setpoint, Kp, Ki, Kd);
  // myController.reverse()               // Uncomment if controller output is "reversed"
  // myController.setSampleTime(10);      // OPTIONAL - will ensure at least 10ms have past between successful compute() calls
  myController.setOutputLimits(48, 255);
  myController.setBias(0.0);
  myController.setWindUpLimits(-10, 10); // Groth bounds for the integral term to prevent integral wind-up

  myController.start();
  // myController.reset();               // Used for resetting the I and D terms - only use this if you know what you're doing
  // myController.stop();                // Turn off the PID controller (compute() will not do anything until start() is called)

  prevChangeRPM = millis();
  Setpoint = 0;

  rpmType = 0;
}

uint32_t mills;
uint16_t currRPM = 0;
float revsSmoothed = 0.0;
void loop()
{
  mills = millis();

  int16_t potVal = analogRead(SETPOINT_POT_PIN);

  // 2, 5, 1
  Kp = map(analogRead(Pterm_POT_PIN), 0, 1023, 0, 100) / 10.0;
  Ki = map(analogRead(Iterm_POT_PIN), 0, 1023, 0, 100) / 10.0;
  // Kd = map(analogRead(Dterm_POT_PIN), 0, 1023, 0, 100) / 10.0;
  
  float bias = map(analogRead(Dterm_POT_PIN), 0, 1023, 0, 2550) / 10.0;
  myController.setBias(bias);
  
  myController.setCoefficients(Kp, Ki, Kd);

  rpmTarget = map(potVal, 0, 1023, 0, MAX_RPM);

  Input = currRPM;
  Setpoint = rpmTarget;

  myController.compute();

  potVal = map(potVal, 0, 1023, -255, 255);
  // Serial.println("pot: " + String(analogRead(POT_PIN)));

  // lowpass / smooth
  RPM_SMOOTH = 0.96 * RPM_SMOOTH + 0.04 * RPM;

  Serial.println(">p-term:" + String(Kp));
  Serial.println(">i-term:" + String(Ki));
  Serial.println(">d-term:" + String(Kd));

  Serial.println(">p-val:" + String(myController.P()));
  Serial.println(">i-val:" + String(myController.I()));
  Serial.println(">d-val:" + String(myController.D()));
  Serial.println(">bias:" + String(bias));

  Serial.println(">RPM (raw): " + String(RPM));
  Serial.println(">RPM (smoothed): " + String(RPM_SMOOTH));
  Serial.println(">Setpoint: " + String(Setpoint));
  Serial.println(">Output: " + String(Output));
  Serial.println(">currRPM: " + String(currRPM));
  Serial.println(">Input: " + String(Input));

  motorA.motorGo(Output);


  if (mills - prevPrintRPM > (1000 / 50))
  {
    // Serial.println(">RPM: " + String(RPM));

    revs /= interruptCount;
    revs = 1.0 / revs;   // rev per us
    revs *= 1000000;     // rev per sec
    revs *= 60;          // rev per min
    revs /= GEARING;     // account for gear ratio
    revs /= ENCODERMULT; // account for multiple ticks per rotation

    if (!isnan(revs))
    {
      revsSmoothed = 0.95 * revsSmoothed + 0.05 * revs;
      // currRPM = (int)(0.9 * currRPM + 0.1 * revs);
      currRPM = (int)revsSmoothed;
    }

    Serial.println(">revs: " + String(revs));
    Serial.println(">revsSmoothed: " + String(revsSmoothed));

    interruptCount = 0;
    revs = 0.0;

    prevPrintRPM = mills;
  }

  delay(1000 / 50);
}

void interruptA()
{
  // motordir = digitalRead(MOTOR_ENCODER_B_PIN);

  // digitalWrite(LED_PIN, HIGH);
  uint32_t currA = micros();
  if (lastA < currA)
  {
    // did not wrap around
    float rev = currA - lastA; // us

    // filter out inrealistic values
    if (rev > 1700)
    {
      interruptCount++;
      revs += rev;

      rev = 1.0 / rev;    // rev per us
      rev *= 1000000;     // rev per sec
      rev *= 60;          // rev per min
      rev /= GEARING;     // account for gear ratio
      rev /= ENCODERMULT; // account for multiple ticks per rotation

      // filter out impossible values
      if (rev < 145)
      {
        RPM = rev;
      }
    }
  }
  lastA = currA;
  // digitalWrite(LED_PIN, LOW);
}

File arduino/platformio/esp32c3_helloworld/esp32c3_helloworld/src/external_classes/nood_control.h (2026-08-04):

#include <Preferences.h>

int16_t noodVals[] = {0, 0, 0, 0};
// kept as float (not int16_t): truncating this on every EMA step causes the average to
// permanently stall short of its target once the per-step increment drops below 1 unit
// (e.g. with noodsAvgSmoothFactor=0.95 and a target of 255, it locks up at exactly 236)
float noodAvgVals[] = {0, 0, 0, 0};

// this is the value amount that we subtract from 127, to allow some deadband between the nood values.
// Effectively, determines the resolution of the noods. 0 is no deadband, 127 is max deadband.
#define NOOD_VALUES_TRANSMISSION_BANDWIDTH 24
#define NOOD_VALUES_BANDWIDTH (127 - NOOD_VALUES_TRANSMISSION_BANDWIDTH)

#define n00d_1a_Pin D8
#define n00d_1b_Pin D1
#define n00d_2a_Pin D10
#define n00d_2b_Pin D0

static const uint8_t nood1a_chan = 0;
static const uint8_t nood1b_chan = 1;
static const uint8_t nood2a_chan = 2;
static const uint8_t nood2b_chan = 3;

// state machine driving the calibration sequence in doThresholdChangeCalibrated()
enum CalibState : int8_t
{
  CALIB_IDLE = 0,    // regular parsing using the last calibrated bounds
  CALIB_LOW,         // sampling+adjusting calibLowerBound
  CALIB_HIGH,        // sampling+adjusting calibUpperBound
  CALIB_AWAIT_RESUME // waiting for throttle to rise back above threshold before resuming regular parsing
};
CalibState calibState = CALIB_IDLE;
CalibState prevCalibState;

void initNoods();
void updateBodyLightValues();
void setBodyLights();
void setn00d(uint8_t chan, uint8_t val);

// calibLowerBound/calibUpperBound are defined further down, persistence helpers need them earlier
extern int16_t calibLowerBound;
extern int16_t calibUpperBound;
void loadCalibBounds();
void checkAndPersistCalibBounds();

void initNoods()
{
  pinMode(n00d_1a_Pin, OUTPUT);
  pinMode(n00d_1b_Pin, OUTPUT);
  pinMode(n00d_2a_Pin, OUTPUT);
  pinMode(n00d_2b_Pin, OUTPUT);

  // nood 1a
  ledcSetup(nood1a_chan, freq, resolution);
  ledcAttachPin(n00d_1a_Pin, nood1a_chan);

  // nood 1b
  ledcSetup(nood1b_chan, freq, resolution);
  ledcAttachPin(n00d_1b_Pin, nood1b_chan);

  // nood 2a
  ledcSetup(nood2a_chan, freq, resolution);
  ledcAttachPin(n00d_2a_Pin, nood2a_chan);

  // nood 2b
  ledcSetup(nood2b_chan, freq, resolution);
  ledcAttachPin(n00d_2b_Pin, nood2b_chan);

  setn00d(nood1a_chan, 0);
  setn00d(nood1b_chan, 0);
  setn00d(nood2a_chan, 0);
  setn00d(nood2b_chan, 0);

  prevCalibState = calibState;

  loadCalibBounds();
}

// static const uint8_t noodIncomingValueOffsets[] = {9, 10, 9, 9}; // original values
static const uint8_t noodIncomingValueOffsets[] = {0, 0, 0, 0}; // original values
// static const uint8_t noodIncomingValueOffsets[] = {11, 10, 10, 10}; // 2026-06 adjusted values
// static const uint8_t noodIncomingValueOffsets[] = {16, 12, 13, 0}; // 2026-06 adjusted values

static constexpr int8_t noodSegmentIdentifiers[] = {0b100, 0b101, 0b110, 0b111}; // upper bits of the nood values
int8_t currSelectedChannel = 0;                                                  // 0-3 for nood1a, nood1b, nood2a, nood2b, -1 for None
int8_t currDetectedChannelSmooth = 0;                                            // 0-3 for nood1a, nood1b, nood2a, nood2b, -1 for None
int8_t currDetectedChannel = 0;
int8_t prevDetectedChannel = 0; // 0-3 for nood1a, nood1b, nood2a, nood2b, -1 for None
int8_t nextChannelIndex = 1;
uint8_t channelChangeCounter = 0;

// crappy way to do this -> refactor using Enum
byte ELRSParseMethod = 3;

void doDirectChange();
void doThresholdChange();
void doThresholdChangeCalibrated();
void doNextItemChange();

float throttleSmoothFactor = 0.12;
int8_t channelChangeThreshold = 1; // number of consecutive readings of a new channel

// calibration state for doThresholdChangeCalibrated() - the sender intermittently transmits
// a lower-bound marker (top 3 bits == 0) followed by an upper-bound value (> 512), letting us
// track the actual analog range instead of trusting SBUS_VAL_MIN/SBUS_VAL_MAX to be exact.
int16_t calibLowerBound = 0;
int16_t calibUpperBound = 1023;
float calibSmoothFactor = 0.9; // smooths new marker readings into the stored bound

// persistence for calibLowerBound/calibUpperBound (NVS via Preferences, the modern
// replacement for the old EEPROM emulation lib): debounced so we don't wear out
// flash while calibration is actively converging every frame.
Preferences noodCalibPrefs;
static const char *NOOD_CALIB_PREFS_NAMESPACE = "noodcal";
static const unsigned long CALIB_BOUNDS_SAVE_DEBOUNCE_MS = 5000;

int16_t calibLowerBoundPrev = calibLowerBound;
int16_t calibUpperBoundPrev = calibUpperBound;
unsigned long calibBoundsChangedAt = 0;
bool calibBoundsPendingSave = false;

void loadCalibBounds()
{
  Serial.println("Loading radio-link calibration bounds from NVS...");

  noodCalibPrefs.begin(NOOD_CALIB_PREFS_NAMESPACE, true); // read-only
  calibLowerBound = noodCalibPrefs.getShort("calibLow", calibLowerBound);
  calibUpperBound = noodCalibPrefs.getShort("calibHigh", calibUpperBound);
  noodCalibPrefs.end();

  calibLowerBoundPrev = calibLowerBound;
  calibUpperBoundPrev = calibUpperBound;
}

void saveCalibBounds()
{
  Serial.println("Saving radio-link calibration bounds to NVS...");

  noodCalibPrefs.begin(NOOD_CALIB_PREFS_NAMESPACE, false); // read-write
  noodCalibPrefs.putShort("calibLow", calibLowerBound);
  noodCalibPrefs.putShort("calibHigh", calibUpperBound);
  noodCalibPrefs.end();
}

// call every frame; debounces writes so calibLowerBound/calibUpperBound only get
// persisted once they've held still for CALIB_BOUNDS_SAVE_DEBOUNCE_MS
void checkAndPersistCalibBounds()
{
  if (calibLowerBound != calibLowerBoundPrev || calibUpperBound != calibUpperBoundPrev)
  {
    calibLowerBoundPrev = calibLowerBound;
    calibUpperBoundPrev = calibUpperBound;
    calibBoundsChangedAt = millis();
    calibBoundsPendingSave = true;
  }
  else if (calibBoundsPendingSave && (millis() - calibBoundsChangedAt >= CALIB_BOUNDS_SAVE_DEBOUNCE_MS))
  {
    saveCalibBounds();
    calibBoundsPendingSave = false;
  }
}

int16_t calibratedThrottle = throttle;
int16_t calibratedThrottleSmoothed = throttleSmoothed;
int16_t calibThreshold = 0.25 * (calibUpperBound - calibLowerBound);

uint16_t calibThrottleSmoothed = 0;
int8_t calibDetectedChannel = 0;
int8_t calibDetectedChannelSmooth = 0;

// DEBUG
bool bListenForIncomingCalibration = true;

float noodsAvgSmoothFactor = 0.95;
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

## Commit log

2023-12-13 add kicad project - import of xiao esp32-c3 schematic and pcb
    [XIAO ESP32C3.kicad_pcb, xiao_esp32c3_schematic.kicad_pcb, xiao_esp32c3_schematic.kicad_sch]
2023-12-15 switch to NeoPixel library, add sinusoidal motor control
2024-01-18 add Arduino Nano test project - rapid testing some separate ideas
2024-01-18 add esp32s2 (wemos d1 mini) project - mainly used for quick esp32 testing
2024-02-03 create xiao esp32c3 symbol
2024-02-03 create v1 of head pcb
    [eel_head_pcbs_assembly.kicad_pcb, eel_head_pcbs_assembly.kicad_sch]
2024-02-03 remove TLC led driver
2024-02-03 Update XIAO ESP32C3.kicad_prl
2024-02-20 Create EelMotor class (copy of ESP32MX1508)
2024-02-20 debug sketch: drive motors with direct ledcWrite
2024-02-20 test sketch: test rgb leds
2024-02-20 mainly: add multi-n00d control (introduces ledc conflicts)
2024-02-22 correct 8-bit to 10-bit analogresolution
    [main.cpp]
2024-02-22 add test sketches exploring esp32 as midi host
2024-02-22 mainly: switch to my own motor class
2024-02-22 add pcb project for xiao + switch
    [eel_esp32_switch_host_board_v01.kicad_pcb, eel_esp32_switch_host_board_v01.kicad_sch]
2024-02-23 add footprint and symbol for DPDT switch
2024-02-23 update xiao esp32-c3 footprint and symbol
2024-02-23 create pcb just for esp32 and on/off switch
    [eel_esp32_switch_host_board_v01.kicad_pcb, eel_esp32_switch_host_board_v01.kicad_sch]
2024-02-27 revert to Espressif v6.4.0. add blink sketch
    [blink.cpp]
2024-02-29 add new pcb design
    [eel_esp32_switch_host_board_v02.kicad_pcb, eel_esp32_switch_host_board_v02.kicad_sch]
2024-02-29 final touches initial pcb design
    [eel_esp32_switch_host_board_v01.kicad_pcb, eel_esp32_switch_host_board_v01.kicad_sch]
2024-02-29 make more room for the pcb holding slot
    [eel_esp32_switch_host_board_v02.kicad_pcb]
2024-02-29 reverse motor direction
2024-03-07 add interactive pcb bom
2024-03-13 fix motor driving bug (wrong ledcWrite line)
2024-04-03 Add head models
    [Head Lower.3mf, Head Upper.3mf]
2024-04-03 Update BOM
2024-04-10 Add tail model
    [Tail.3mf]
2024-04-10 add xiao esp32s3 project for driving dummy transmitter (midi)
2024-04-10 add undercarriage 3MFs
    [undercarriage axle.3mf, undercarriage wheel.3mf]
2024-04-10 Create Main pcb slide switch end cap.3mf
    [Main pcb slide switch end cap.3mf]
2024-04-10 fix ledcWrite not working
2024-04-17 add motor wheel model
    [motor wheel v01.3mf]
2024-04-17 update some eel models (print settings)
    [Head Lower.3mf, Mouth Light Guide.3mf, Segment with n00d.3mf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]
2025-11-19 remove Toad-related Arduino sketches from repo
2025-11-19 update some Kicad symbols and footprints
2025-11-19 update Kicad project (probably nothing)
    [eel_esp32_switch_host_board_v02.kicad_sch]
2025-11-21 Add operator manual and schematics
    Updated links in the README for operator manual and added schematic.
2025-11-21 Remove duplicate PCB designs entry
    Removed duplicate PCB designs entry from README.
